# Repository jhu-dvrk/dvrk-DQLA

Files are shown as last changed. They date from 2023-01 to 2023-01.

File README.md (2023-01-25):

# DQLA
PCB design files for Dual Quad Linear Amplifier (DQLA) system, which
allows a single FPGA board to drive two QLAs.

This repository contains the design files for two boards:

* `DQLA-F`:  FPGA Interface Board
* `DQLA-Q`:  Dual QLA Interface Board

The basic design is that the FPGA board is mounted on the DQLA-F board,
which routes the I/O lines to the DQLA-Q board (via two 50-pin flat flex cables).
The DQLA-Q is mounted on top of two QLA boards.

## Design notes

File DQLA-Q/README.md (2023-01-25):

# DQLA-Q
Design files for Dual QLA Interface board, used in Dual Quad Linear Amplifier (DQLA) system

This board receives the FPGA I/O signals via two 50-pin flat flex cables and routes them to the two QLAs. Note that it contains two Max7301 I/O expanders that provide additional I/O.

* `DQLA-Q.PrjPCB`: Altium Designer project file
* `Snn.SchDoc`: schematics (Altium Designer format)
* `DQLA-Q.PcbDoc`: PCB layout (Altium Designer format)
* `DQLA-Q-Schematics.pdf`: PDF of schematics
* `DQLA-Q-BOM.xls`: Bill of Materials (Microsoft Excel format)
* `Panel`: Subdirectory with panel design, including PCB fabrication and assembly files
 
## Release Notes

* Rev 1.1: Build #1 (50 boards)

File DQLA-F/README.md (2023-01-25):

# DQLA-F
Design files for FPGA Interface board, used in Dual Quad Linear Amplifier (DQLA) system

This board routes the I/O signals from the attached FPGA board to the two 50-pin flat flex cables,
which connect to the DLQA-Q board and ultimately to the two QLAs. It also contains the safety
circuit, including safety relay, safety chain connectors and status LEDs.

* `DQLA-F.PrjPCB`: Altium Designer project file
* `S01.SchDoc`: schematics (Altium Designer format)
* `DQLA-F.PcbDoc`: PCB layout (Altium Designer format)
* `DQLA-F-Schematics.pdf`: PDF of schematics
* `DQLA-F-BOM.xls`: Bill of Materials (Microsoft Excel format)
* `Panel`: Subdirectory with panel design, including PCB fabrication and assembly files
 
## Release Notes

* Rev 1.1: Build #1 (50 boards)

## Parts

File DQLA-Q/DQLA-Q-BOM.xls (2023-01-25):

 | DQLA-Q
 | (DQLA Dual QLA Interface Board)
 | Bill Of Materials
 | 2023-01-23
Revision: |  | 1.1
Seq | Qty. | Ref Des (Multi-2) | Description | Package | Manufacturer | Notes | Manufacturer Part # | Distributor | Distributor Part # | Avcon Part # | Est. Unit $ | Extended Cost
1 | 12 | C1-10, C13 | CAP, 0.1uF 10% 16V X7R, 0402 | 0402 | Generic | 2 | GRM155R71C104KA88D | Digikey |  |  | 0.02 | 0.24
2 | 3 | C11, C12 | CAP, 22uF 20% 16V X7R, 0805 | 0805 | Generic | 2 | GRM21BZ71A226ME15L | Digikey | 490-GRM21BZ71A226ME15LCT-ND |  | 0.17 | 0.51
3 | 4 | D1-2 | LED, Red, 0805 | LED-0805 | Generic | 2 | LTST-C170GKT | Digikey | 160-1179-1-ND |  | 0.18 | 0.72
4 | 2 | D3 | LED, Green, 0805 | LED-0805 | Generic | 2 | LTST-C170EKT | Digikey | 160-1178-1-ND |  | 0.18 | 0.36
5 | 4 | J1-2 | CONN, Socket, 2x22 Pos, Vertical, 2MM | TH | Samtec | 2 | ESQT-122-02-L-D-560 | Samtec | ESQT-122-02-L-D-560 | 026-0844-00 | 5.72 | 22.88
6 | 2 | J3-4 | CONN, FPC, 50 Pin, 0.5mm, XF3M-5015 | XF3M-5015 | Omron |  | XF3M-5015-1B | Digikey | OR1185CT-ND |  | 2.57 | 5.14
7 | 2 | Q1 | MOSFET, Dual N-Chan, 20V, 800mA, SQ1912EH | SC70-6-NP | Vishay | 2 | SQ1912EH-T1_GE3 | Digikey | SQ1912EH-T1_GE3CT-ND | 024-2190-SM | 0.19 | 0.38
8 | 52 | R1-8, R9-30 | RES, 49.9, 1%, 1/16W, 0402 | 0402 | Generic | 2 |  | Digikey | P49.9LCT-ND |  | 0.02 | 1.04
9 | 6 | R31-33 | RES, 150, 1%, 1/10W, 0603 | 0603 | Generic | 2 |  | Digikey | 541-39.0KHCT | 020-1500-51/603 | 0.04 | 0.24
10 | 2 | R34 | RES, 39.0K, 1%, 1/16W, 0402 | 0402 | Generic | 2 |  | Digikey | P39.0KLCT-ND |  | 0.02 | 0.04
11 | 3 | RN1, RN2 | RES ARRAY, 10K, 4 DIS, 5%, SM 0.032 | R-SM-8/32 | CTS | 2 | 742C083103JPTR | Digikey | 742C083103JPCT-ND | 020-1002-6RASM | 0.02 | 0.06
12 | 8 | U1-8 | IC, Dual Schmit Trig. Buffer, 74LVC2G17 | SC70-6 | TI | 2 | SN74LVC2G17DCK3 | Digikey | 296-SN74LVC2G17DCK3CT-ND |  | 0.36 | 2.88
13 | 2 | U9-10 | IC, 2:1 Mux, 74LVC1G157 | SC70-6 | NXP | 2 | 74LVC1G157GW,125 | Digikey | 1727-3491-2-ND |  | 0.20 | 0.40
14 | 2 | U11 | IC, IO Expander, 28 Port, SPI, MAX7301-QFN | QFN-40-6mm | Maxim |  | MAX7301ATL+T | Digikey | MAX7301ATL+CT-ND |  | 8.59 | 17.18
15 | 1 |  | PCB, DQLA-Q, Rev 1.1 |  |  |  |  |  |  |  | 35.00 | 35.00
 |  |  |  |  |  |  |  |  |  | Estimated total Cost: |  | $87.07
Notes:
 | ● | Reference designators highlighted in green are replicated 2 times on the PCB, as Uxx-1 and Uxx-2.
 | ● | Text highlighted in red is highlighted to draw attention to the value/parameter and does not carry any special meaning.
 | ● | Component prices shown are the best guess at the time of updating this BOM, assuming Qty ~100 boards. Actual prices may be higher or lower depending upon a number of factors.
 | ● | Unless specified otherwise, the only substitutions allowed are substituting identical part number parts from a different manufacturer.
 | NS | No substitutions of any kind are allowed.
 | 1
 | 2 | Any component in an identical package that meets or exceeds all the paramaters specified in the description can be substituted.

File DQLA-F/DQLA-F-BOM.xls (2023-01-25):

 | DQLA-F
 | (DQLA FPGA Interface Board)
 | Bill Of Materials
 | 2023-01-23
Revision: |  | 1.1
Seq | Qty. | Ref Des | Description | Package | Manufacturer | Notes | Manufacturer Part # | Distributor | Distributor Part # | Avcon Part # | Est. Unit $ | Extended Cost
1 | 1 | D1 | DIODE, Dual Zener, 6.8V, SOT-23, AZ23C6V8 | SOT-23 | Vishay | 3 | AZ23C6V8-E3-08 | Mouser | 78-AZ23C6V8-E3-08 | 024-0514-SM | 0.15 | 0.15
2 | 1 | D2 | LED, Quad, Green | LED-3MM-QUAD | Kingbright | 3 | WP914CK/4GDT | Digikey | 754-1286-ND | 024-6383-00 | 1.25 | 1.25
3 | 2 | J1-2 | CONN, Header, 2x22 Pos, Vertical, 2MM. | HDR-22x2-2MM | Samtec | 3 | TMM-122-03-L-D | Samtec | TMM-122-03-L-D | 026-0846-00 | 6.65 | 13.31
4 | 2 | J3-4 | CONN, FFC, 50-pin, XF3M | SM-0.5MM | Omron | 5 | XF3M-5015-1B | Digikey | OR1185CT-ND |  | 2.92 | 5.83
5 | 1 | J5 | CONN, WR-TBL Series 313, 4-pin | TH | Wurth | 4 | 691313510004 | Digikey | 732-2072-ND |  | 0.66 | 0.66
6 | 1 | J6 | CONN, WR-TBL Series 313, 5-pin | TH | Wurth | 4 | 691313510005 | Digikey | 732-2073-ND |  | 1.03 | 1.03
7 | 1 | J7 | CONN, Header, 3 Pos, Vertical 0.100 | TH | Tyco | 2, 3 | 640456-3 | Digikey | A19470-ND | 026-0083-00 | 0.34 | 0.34
8 | 2 | J8-9 | CONN, Header, 2 Pos, Vertical 0.100 | TH | Tyco | 2, 3 | 640456-2 | Digikey | A1921-ND | 026-0080-00 | 0.30 | 0.60
9 | 1 | Q1 | MOSFET, Dual N-Chan, 20V | SOT-363 | Vishay | 2, 3 | SQ1912EH | Digikey | Q1912EH-T1_GE3CT-ND | 024-2190-SM | 0.19 | 0.19
10 | 26 | R1-26 | RES, 49.9, 1%, 0402 | 0402 | Generic | 2 |  |  |  |  | 0.0005 | 0.01
11 | 1 | R27 | RES, 1.00K, 1%, 0402 | 0402 | Generic | 2 |  |  |  |  | 0.0006 | 0.0006
12 | 4 | R28-31 | RES, 4.99K, 1%, 0402 | 0402 | Generic | 2 |  |  |  |  | 0.0006 | 0.0024
13 | 1 | U1 | RELAY, 5V, DPDT | DIP | TE Conn | 3 | IM03TS | Digikey | PB1094-ND |  | 3.44 | 3.44
14 | 1 |  | PCB, DQLA-F, Rev 1.1 |  |  |  |  |  |  |  | 15.00 | 15.00
 |  |  |  |  |  |  |  |  |  | Estimated Total Cost: |  | $41.81
Notes:
 | ● | Text highlighted in red is highlighted to draw attention to the value/parameter and does not carry any special meaning.
 | ● | Component prices shown are the best guess at the time of updating this BOM, assuming Qty ~100 boards. Actual prices may be higher or lower depending upon a number of factors.
 | ● | Unless specified otherwise, the only substitutions allowed are substituting identical part number parts from a different manufacturer.
 | NS | No substitutions of any kind are allowed.
 | 1
 | 2 | Any component in an identical package that meets or exceeds all the paramaters specified in the description can be substituted
 | 3 | Parts also used on QLA
 | 4 | Parts also used on dRAC
 | 5 | Compatible with Molex Premo-Flex 15266 series cables

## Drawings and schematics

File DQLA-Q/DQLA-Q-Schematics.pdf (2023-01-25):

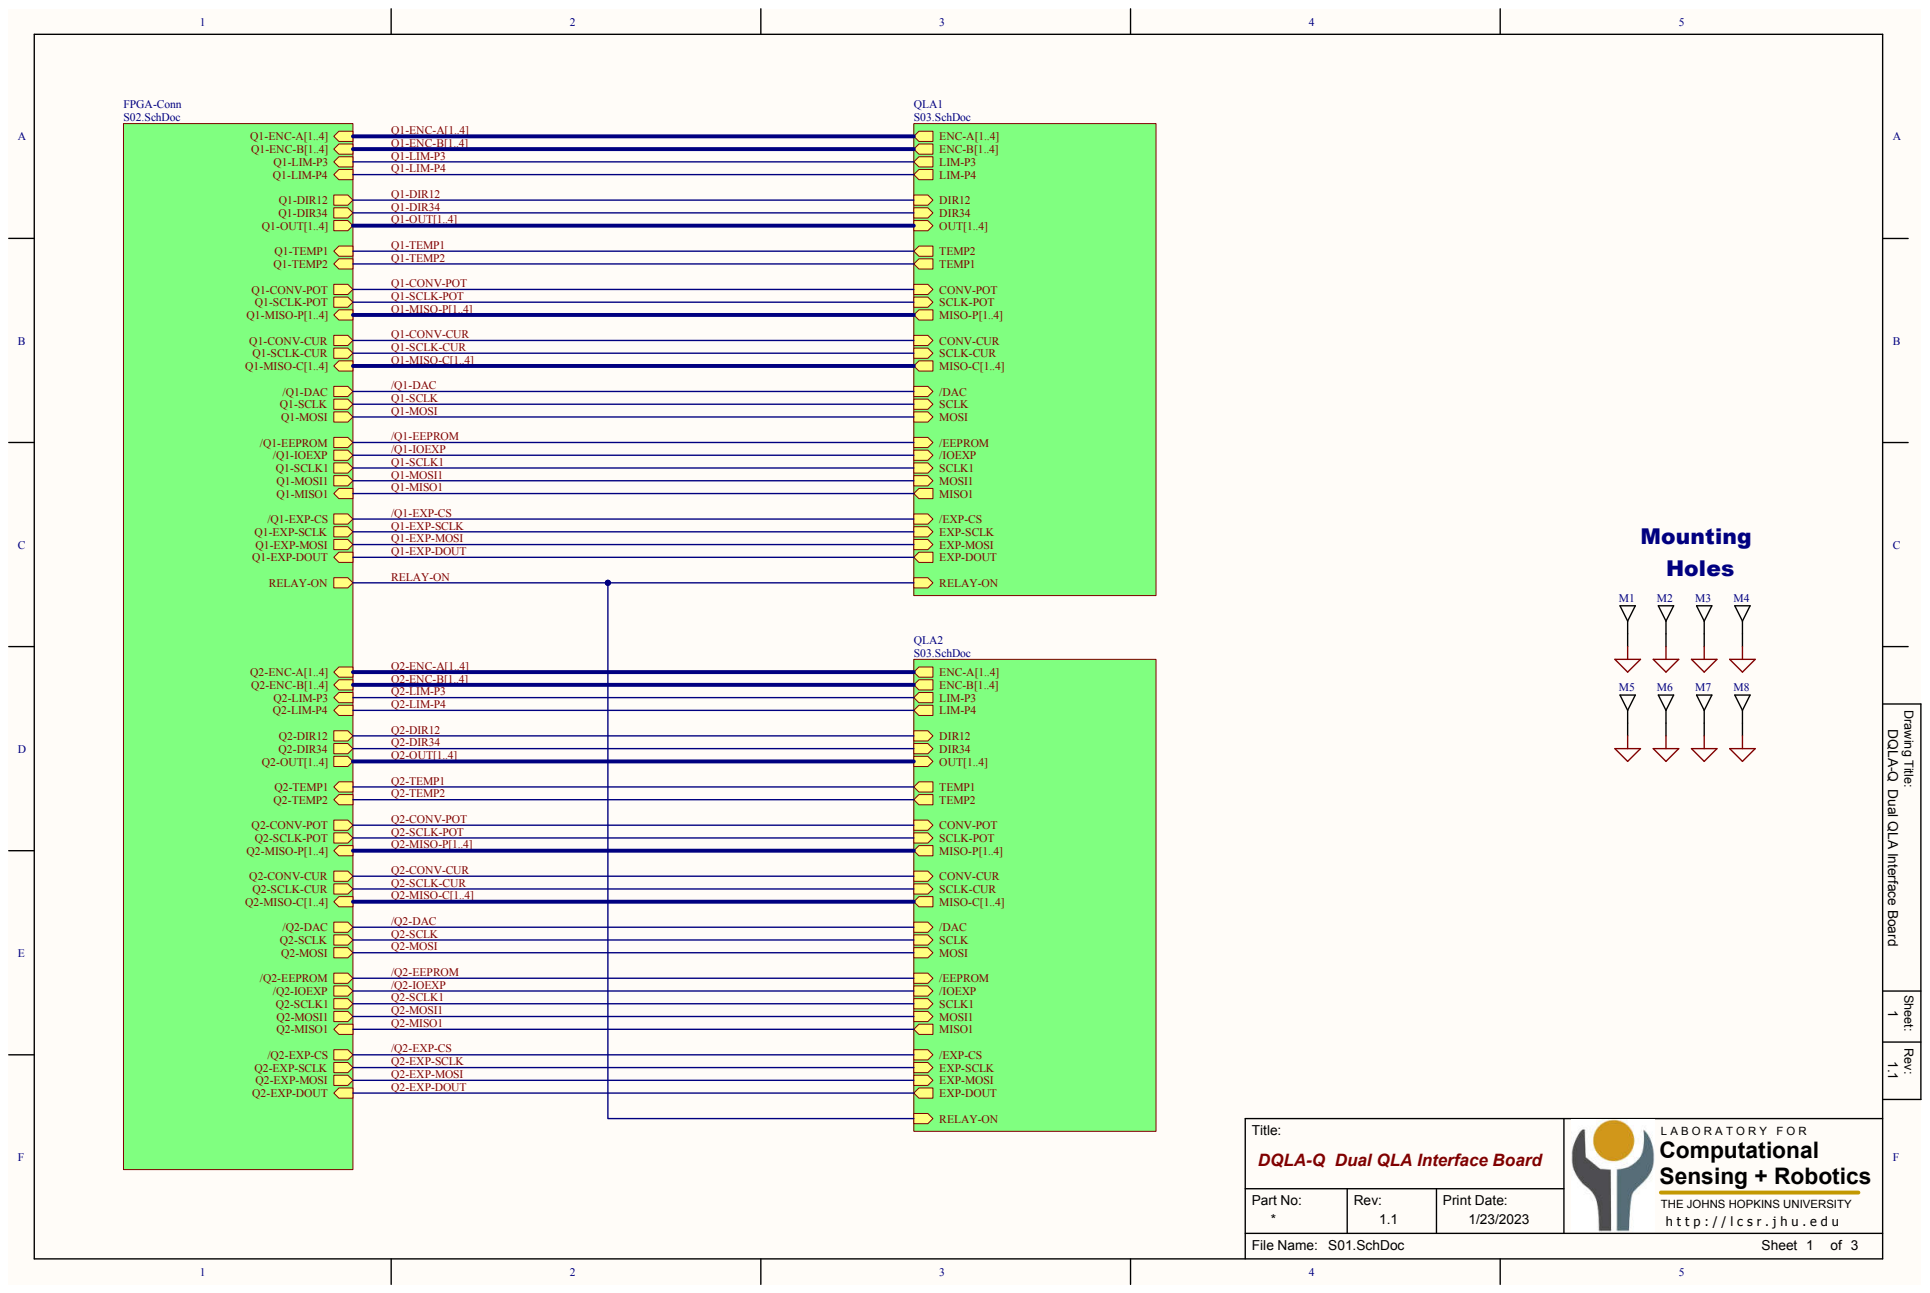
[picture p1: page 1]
Sheet; FDCBA; CBA; Q2-DIR34; Q1-CONV-CUR; /Q1-EXP-CS; /Q2-EXP-CS; Q2-LIM-P4; Q1-DIR12; Q1-LIM-P4; Q1-SCLK-CUR; Q1-DIR34; Q2-EXP-DOUT; Q1-MOSI1; RELAY-ON; Q1-CONV-POT Q1-SCLK-POT; Q2-DIR12; Q2-OUT[1..4]; Q2-LIM-P3; /Q1-DAC; Q1-MISO-P[1..4]; Q2-MISO-P[1..4]; Q1-LIM-P3; Q1-TEMP2; /Q1-IOEXP; /Q1-EEPROM; Q2-TEMP2; Q2-TEMP1; /Q2-DAC; /Q2-IOEXP; Q2-ENC-A[1..4]; Q1-MOSI; Q1-OUT[1..4]; Q1-MISO-C[1..4]; /Q2-EEPROM; Q2-MISO-C[1..4]; Q2-ENC-B[1..4]; Q1-ENC-B[1..4]; Q2-MOSI; Q1-EXP-DOUT; Q1-ENC-A[1..4]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

Drawing Title: Rev: Sheet:

1 DQLA-Q Dual QLA Interface Board 1.1

Title: DQLA-Q Dual QLA Interface Board | L A B O R A T O R Y F O R Computational Sensing + Robotics THE JOHNS HOPKINS UNIVERSITY h t t p : / / l c s r . j h u . e d u

Part No: * | Rev: | Print Date:

File Name: S01.SchDoc

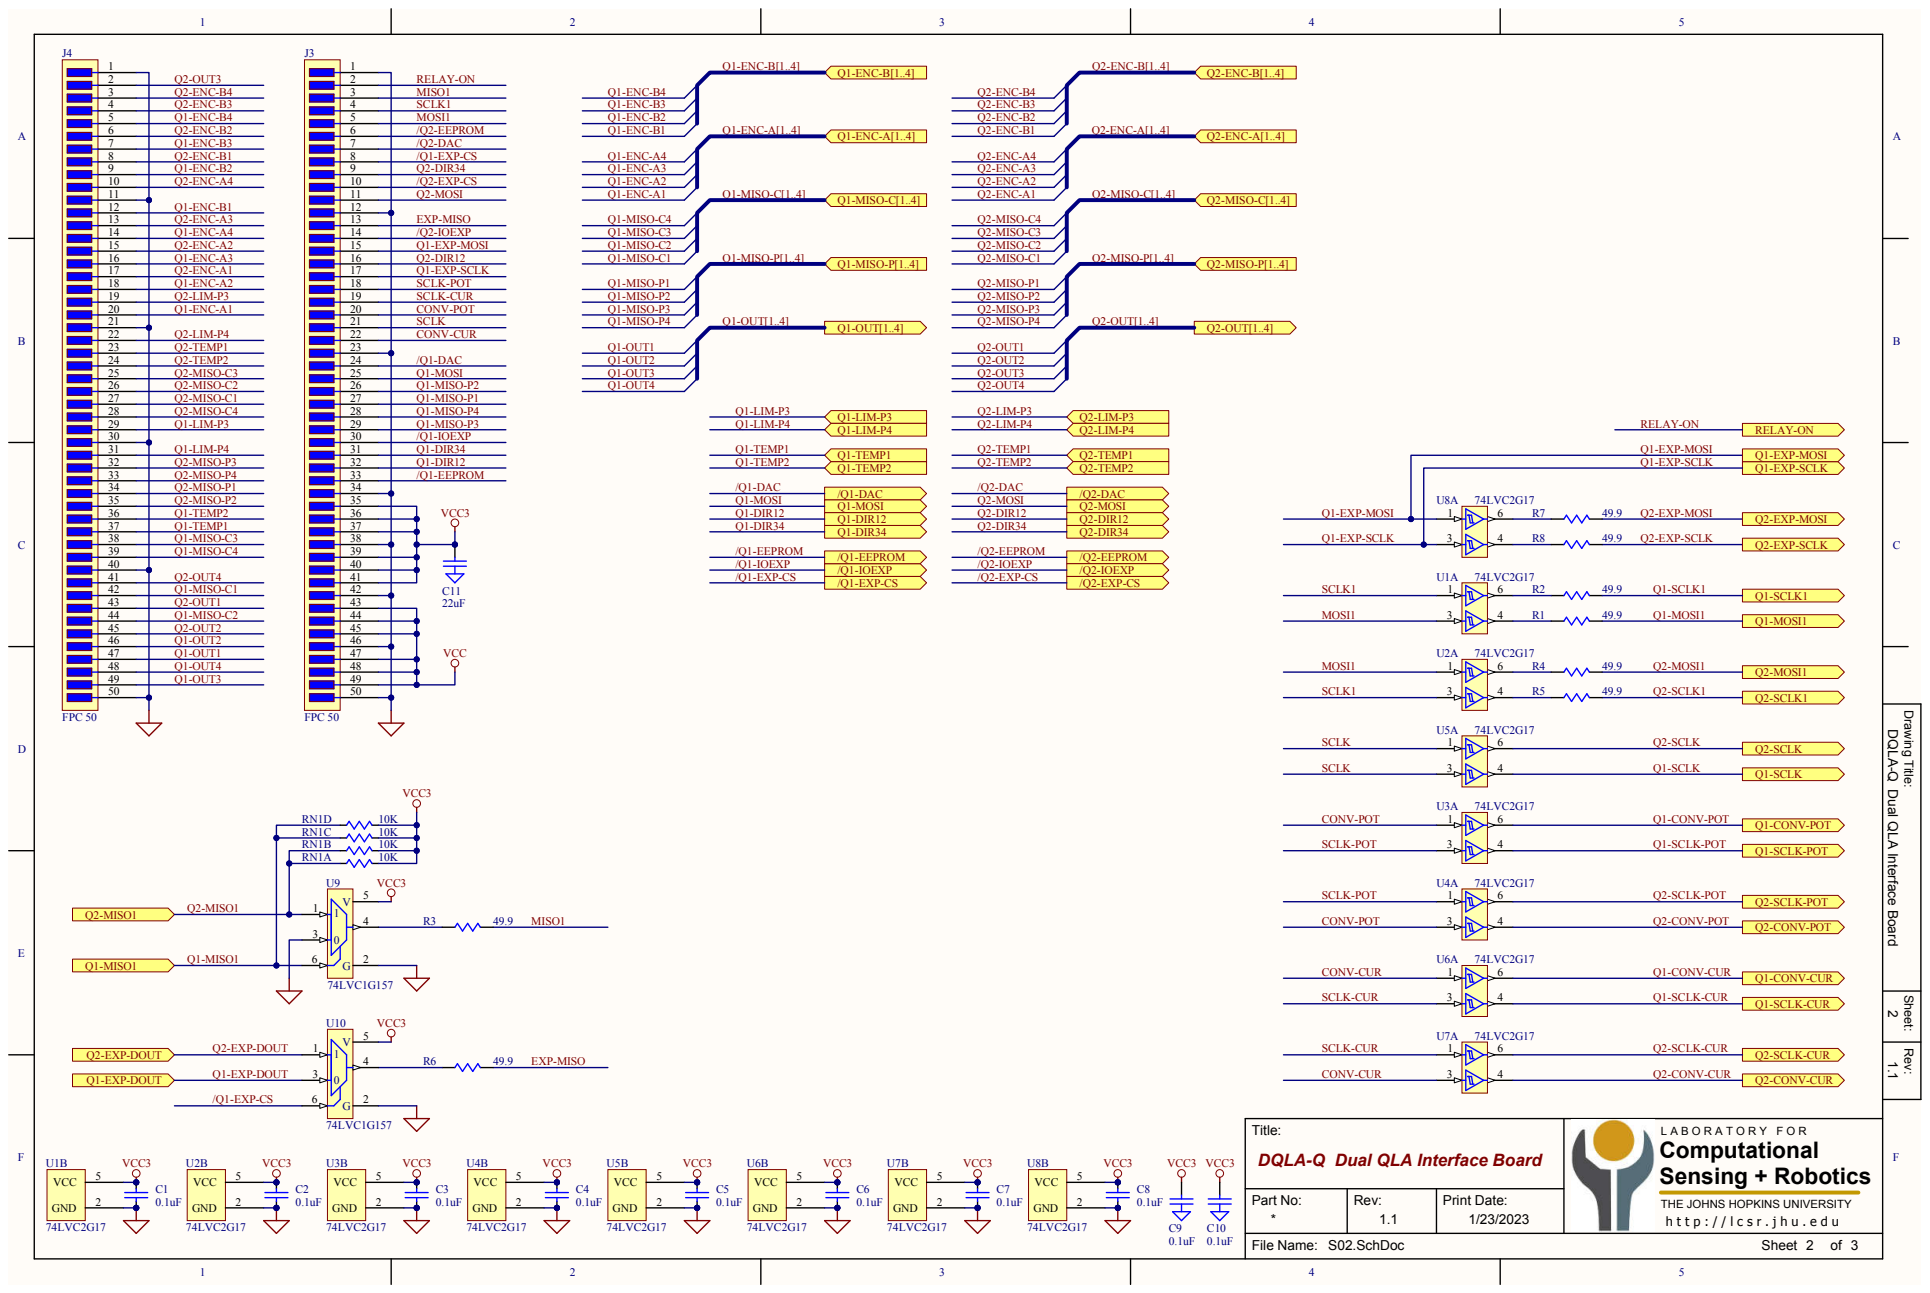
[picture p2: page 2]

Q1-EXP-MOSI
Q1-EXP-SCLK

Drawing Title: Rev: Sheet:

Dual QLA Interface Board 1.1

Title:
DQLA-Q Dual QLA Interface Board

# Connectors to QLA

8 P16 | 9 P17 | 10 P18 | 12 P19 | 13 P20 | 14 P21 | 15 P22 | 16 P23 | 17 P24 | 18 P25 | 19 P26 | 21 P27 | 22 P28 | 23

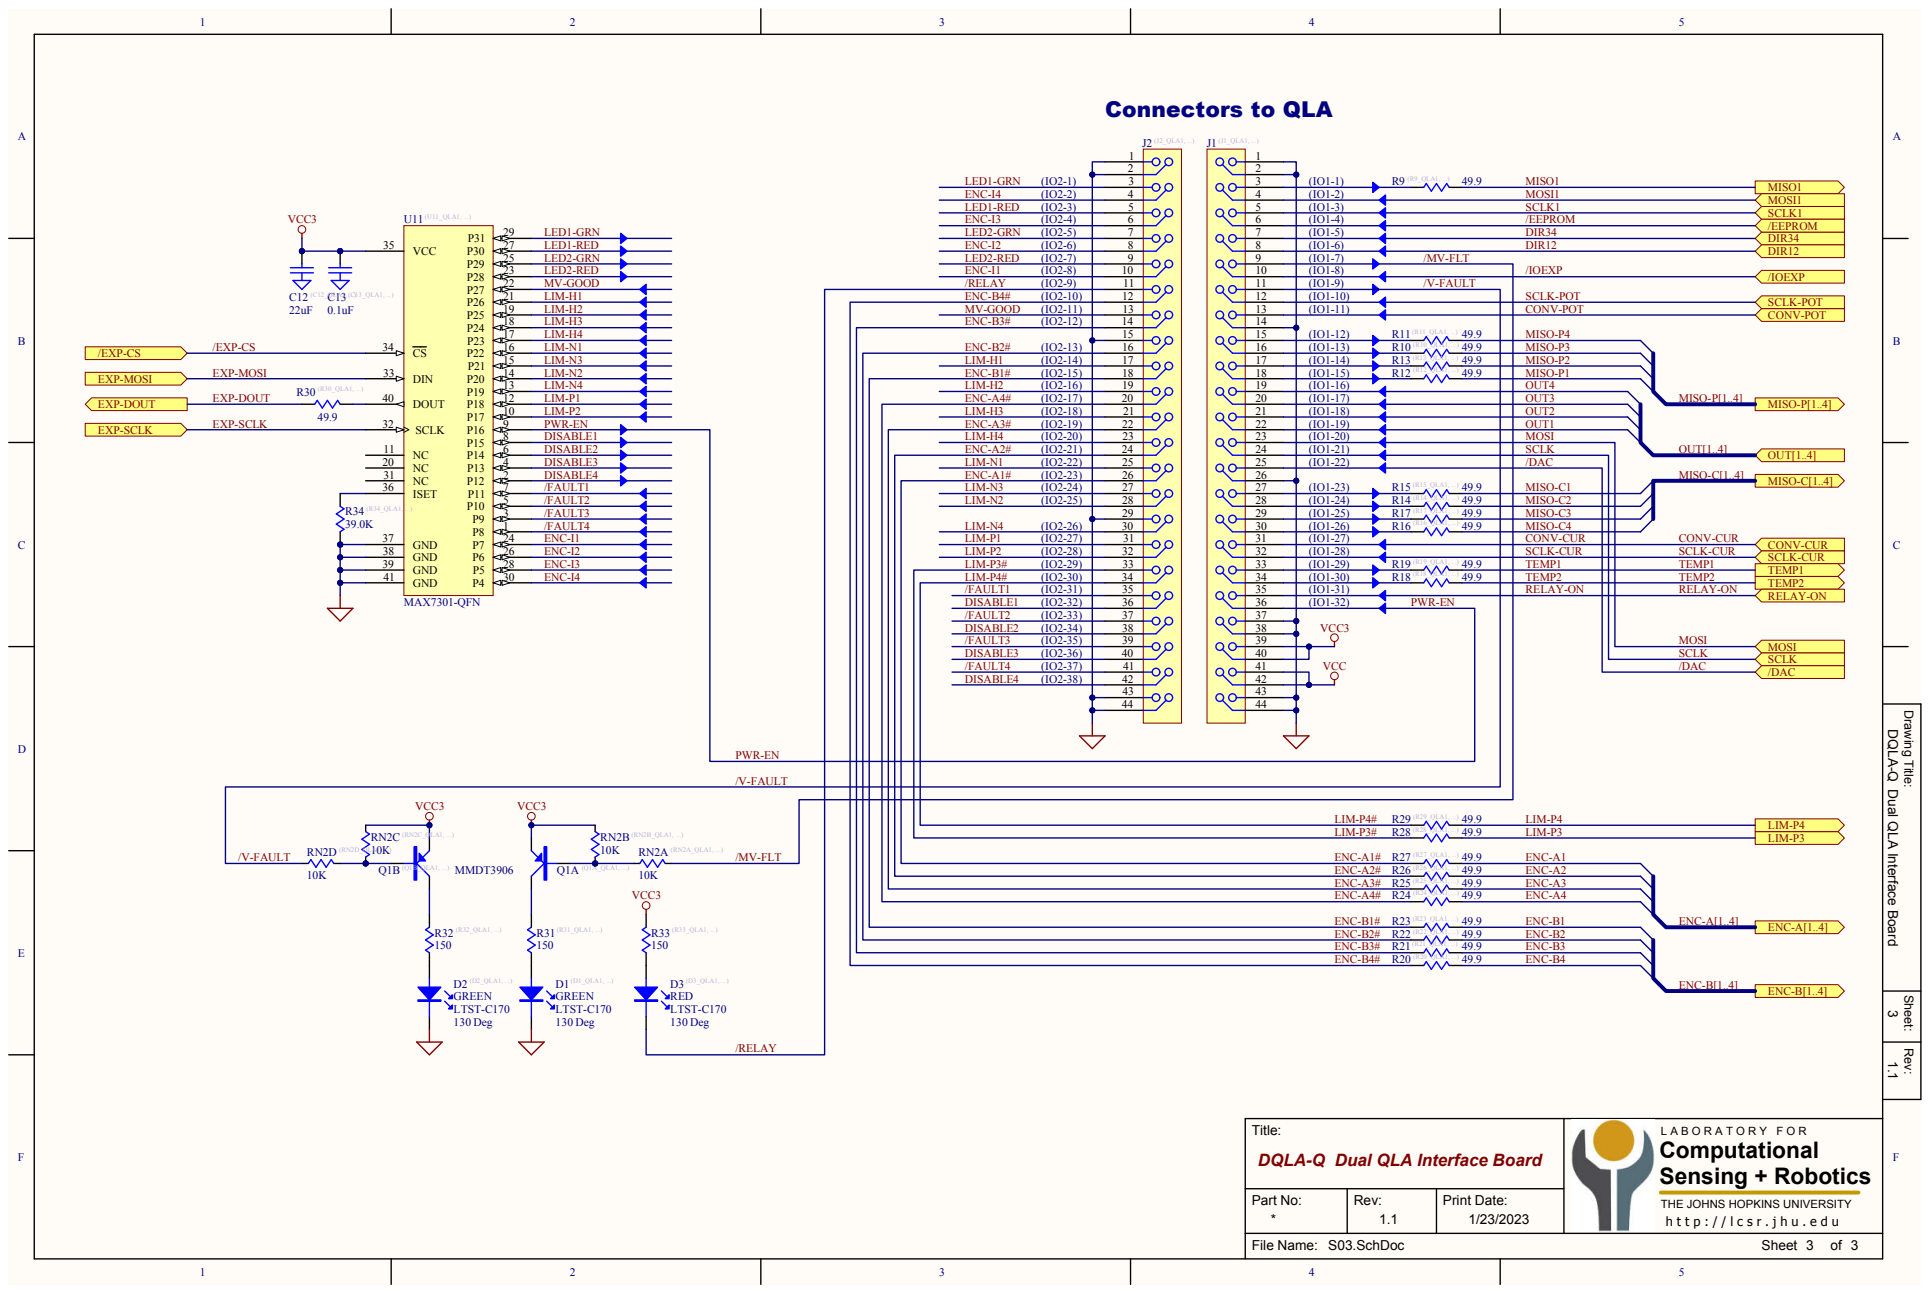
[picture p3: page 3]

Drawing Title: Rev: Sheet:

3 DQLA-Q Dual QLA Interface Board 1.1

Title:
DQLA-Q Dual QLA Interface Board

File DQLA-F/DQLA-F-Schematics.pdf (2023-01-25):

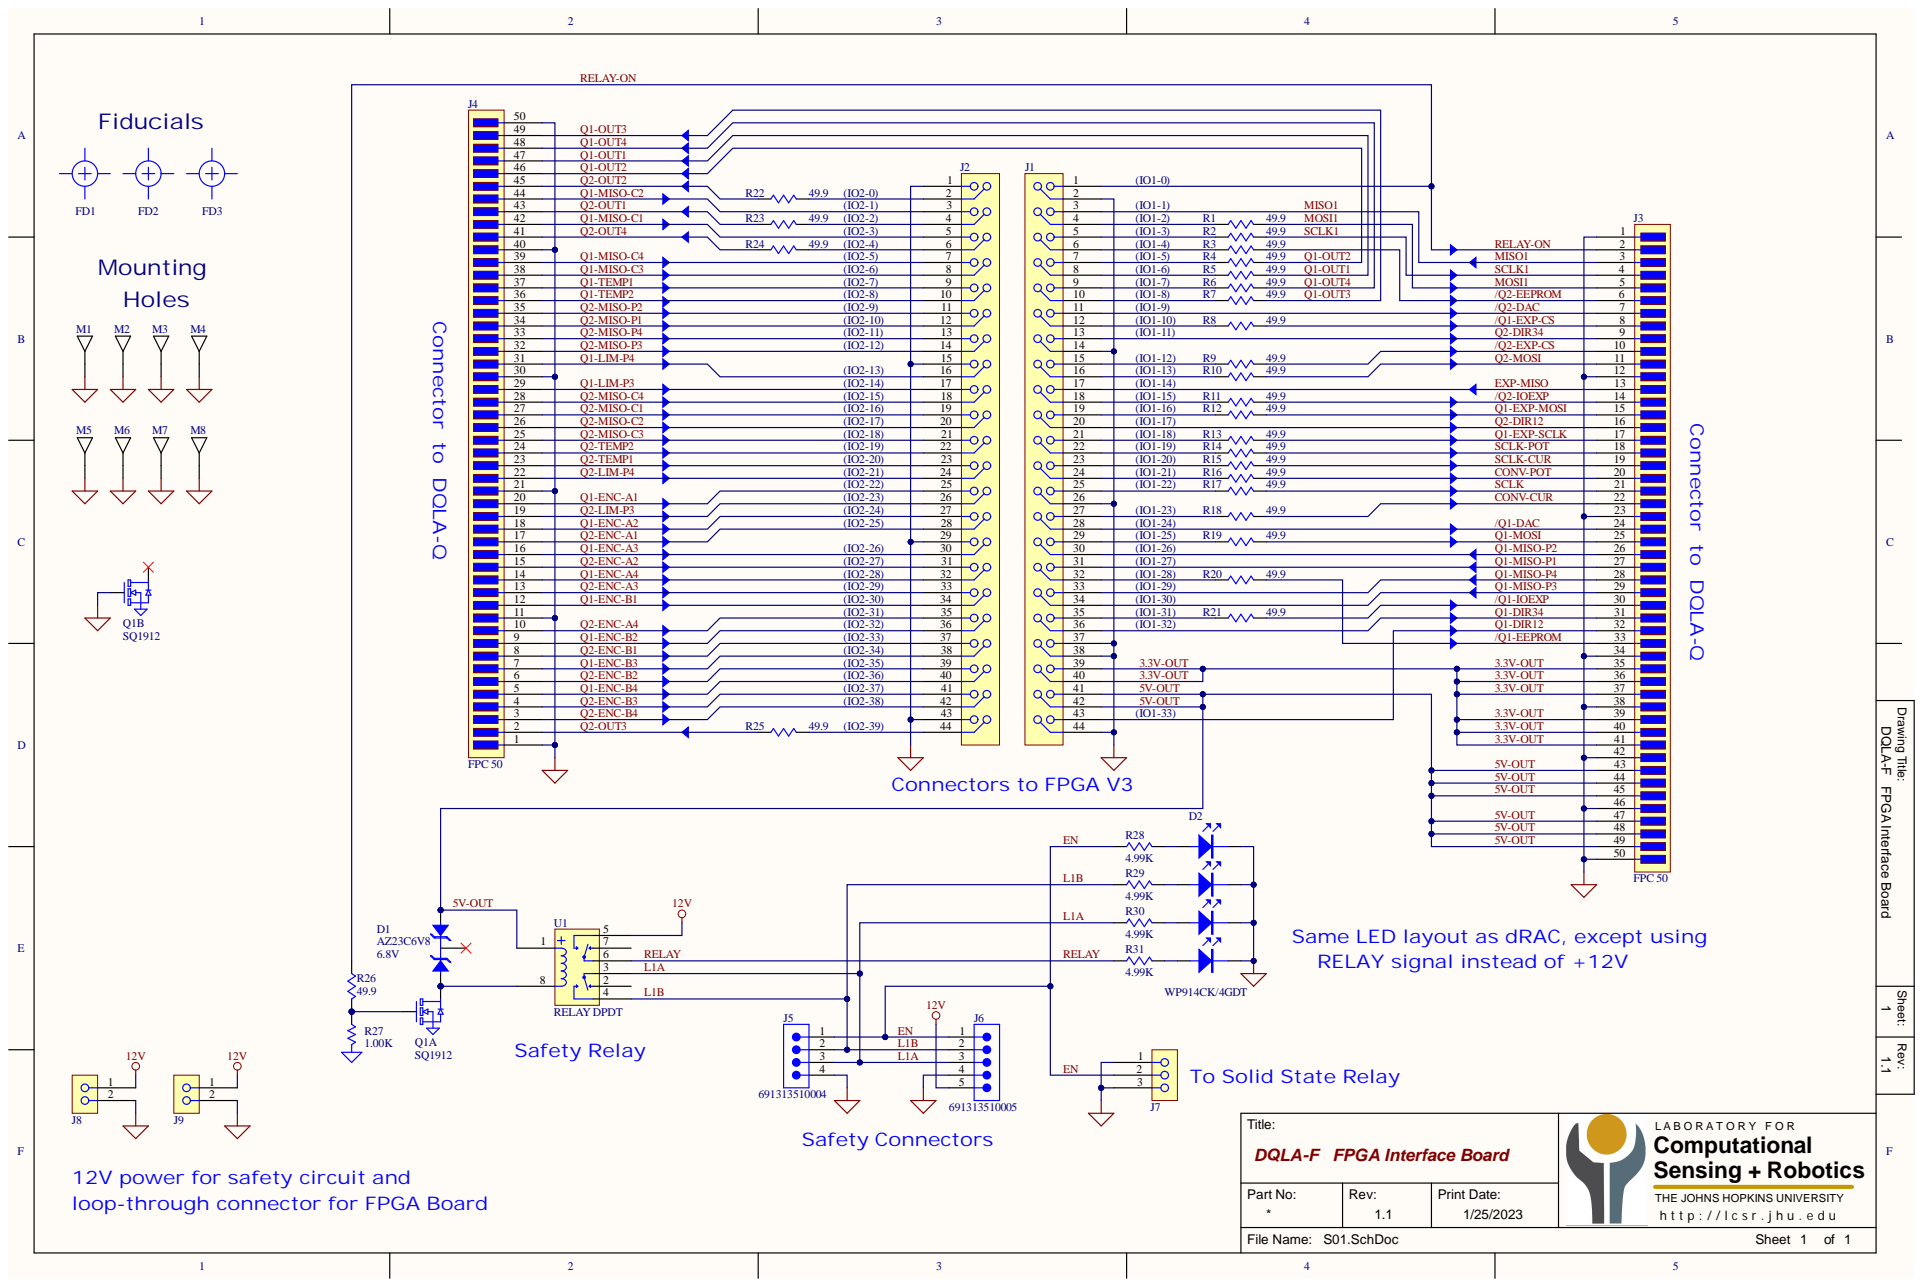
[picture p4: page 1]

9 SC L K 1
9 | R E L AY-O N

Drawing Title: Rev: Sheet:

1 DQLA-F FPGA Interface Board 1.1

5V -O U T | 44
5V -O U T | 45
5V -O U T | 46

5V -O U T | 48
5V -O U T | 49

L1A L1B ENEN

Same LED layout as dRAC, excep
RELAY signal instea

through connector for FPGA Board

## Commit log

2023-01-25 Initial commit (Rev 1.1)
    [DQLA-F-BOM.xls, DQLA-F.PcbDoc, DQLA-F.PrjPcb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]
2023-01-25 Initial commit of DQLA-Q (Rev 1.1); update to DQLA-F assembly ReadMe
    [DQLA-Q-BOM.xls, DQLA-Q.PcbDoc, DQLA-Q.PrjPcb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]
